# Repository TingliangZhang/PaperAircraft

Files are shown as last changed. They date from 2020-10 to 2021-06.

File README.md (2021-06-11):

# PaperAircraft
https://en.wikipedia.org/wiki/Paper_plane

## V3版本

全新版本

电磁舵机+8mm空心杯+1S小锂电+电磁舵机接收机（集成5A电调）

2.4G带两路电磁舵驱动 5通道微型接收机 Futaba S-FHSS

https://item.taobao.com/item.htm?id=544533760584

遥控器兼容 S-FHSS即可

https://futabausa.com/product/14sg/

## 纸飞机

https://www.poweruptoys.com/

https://www.indiegogo.com/projects/powerup-4-0-smartphone-controlled-paper-airplane--2#/

https://item.taobao.com/item.htm?id=598983848365

https://detail.1688.com/offer/623588992739.html

看了这么多产品，最后还是要自己写飞控。通信用蓝牙或者Wifi，NanoBLESense可能又要用起来了。

https://item.taobao.com/item.htm?id=580652831242

小巧的7.8g高压锂电还是要用的

1.7g微型舵机

https://item.taobao.com/item.htm?id=610628423127

参考F3P和F1D

F3P

https://ultralight.tech/

https://www.bilibili.com/video/BV1Yk4y1971W

F1D

https://www.bilibili.com/video/BV1Q5411s7f6

可以考虑用共轴反桨，但是重量有点大，如果能开发微型共轴反桨，可以搞简单的直升机雪花。

## 一些想法

激光切割卡纸

BLE广播 mesh

## V1方案

元件选型

主控板：[Arduino Nano 33 BLE Sense](https://store.arduino.cc/usa/nano-33-ble-sense-with-headers)

3.3V能否接3.8V+存疑，考虑换DCDC芯片，但是[MPM3610](https://www.monolithicpower.cn/cn/mpm3610.html)的封装是节省空间的 QFN-20 (3mmx5mmx1.6mm)封装，很难找到相应的芯片以及更换。此路不通

外接一块3.8v-3.3v DCDC转换模块，找了一圈淘宝，找到DM13B-3.3，可以升降压。

[Arduino Nano 33 BLE](https://store.arduino.cc/usa/nano-33-ble)更便宜

新解决方案！电调上面的UBEC，UBEC输出:5.2V 2A（正负0.1V），原本给接收机用的，可以用来驱动Arduino！

电池：[Happymodel 3.8V 300mAh 30C 1-2S Lipo Battery PH2.0 Plug for Mobula6/7](http://www.happymodel.cn/index.php/2018/09/22/happymodel-3-8v-300mah-30c-1-2s-lipo-battery-ph2-0-plug-for-mobula7/)

https://item.taobao.com/item.htm?id=580652831242

Capacity:300mAh

Voltage:3.8v

Continuous Discharge Rate: 30C

Instantaneous discharge rate: 60C

Size: 57mmx12mmx7mm

Weight: 6.5g

Connector: PH2.0

充电器：[Happymodel Mobula7 FPV Racing Drone Spare Part 1S06 6 Way Lipo/LIHV Battery Charger](http://www.happymodel.cn/index.php/2018/08/31/happymodel-ur65-fpv-racing-drone-spare-part-1s06-6-way-lipolihv-battery-charger/)

https://item.taobao.com/item.htm?id=566199133982

4.20v cell charging cutoff (+- 0.5% margin of error) for 1S Lipo Battery

4.35v cell charging cutoff (+- 0.5% margin of error) for 1S 3.8V LIHV Battery

电机：暂时使用劣质的1.72块钱一个的[高速航模电机马达双环强磁716空心杯电机3.7V暴力50000转包邮](https://item.taobao.com/item.htm?id=535704086171)

规格:7x16x0.8mm 额定电压：3.7V 启动电压：0.15V 额定电流：800mA 额定转速：34000

舵机：[AFRC-D1302微型1.7g舵机MINI精致1.9g航模室内飞机直升机数字舵机 ](https://item.taobao.com/item.htm?spm=a1z09.2.0.0.2afc2e8doX2vub&id=607309316067)

尺寸:13.5 x 6.2 x 20.1 mm

重量:1.7g(不含线)

工作电压:3.7~5.0V

扭力:

3.7V：2.08 oz-in (0.15 kg-cm)

4.2V：2.36 oz-in (0.17 kg-cm)
速度:

3.7V：0.06 sec/60°

4.2V：0.04 sec/60°

出线: JST1.25mm L=110mm （棕-，红+，橙S）

直线电机：[AFRC-D1015直线舵机1.5克微型轻量迷你1.5g数字舵机](https://item.taobao.com/item.htm?spm=a1z09.2.0.0.2afc2e8doX2vub&id=611726187447)

尺寸:21.4 x 15.2 x 6.0 mm

重量:1.5g(不含线)

出线: JST1.25mm L=100 mm （红+，黑-，白S）；JST1.0mm,JR,Futaba L=100 mm （棕-，红+，橙S）

工作电压:3.7~6.0V

工厂默认行程为7mm/900~2100us

电机驱动：[1S超小微型单向有刷电调航模飞机固定翼空心杯电机专用驱动控制器](https://item.taobao.com/item.htm?id=548195280709)

最多能接4个空心杯电机;N20,N30,N50,131,180电机可以接2只.。

输入电池电压:2.2V-5.2V（超过5.5V烧电调）.

最大输出电:流20A.

UBEC输出:5.2V 2A.（正负0.1V）

## V2做PCB方案

自己画：STM32 蓝牙 IMU

or ESP32WROOM + IMU

STM32选型：STM32G031K8T6 STM32G031J6M6

PCB板上外设：

1. 蓝牙透传
2. IMU（目前可选）
3. 3.8v-3.3v降压稳压芯片
4. 空心杯电机驱动芯片
5. 电池电机舵机接口

具体选型

### DCDC芯片

TI电源解决方案[选型](https://www.ti.com/design-resources/design-tools-simulation.html)网站

[WEBENCH Power Designer](http://webench.ti.com/power-designer/switching-regulator)

[TLV62569DBVR](https://item.szlcsc.com/153167.html) 2A

[TLV62568DBVR](https://item.szlcsc.com/174600.html) 1A

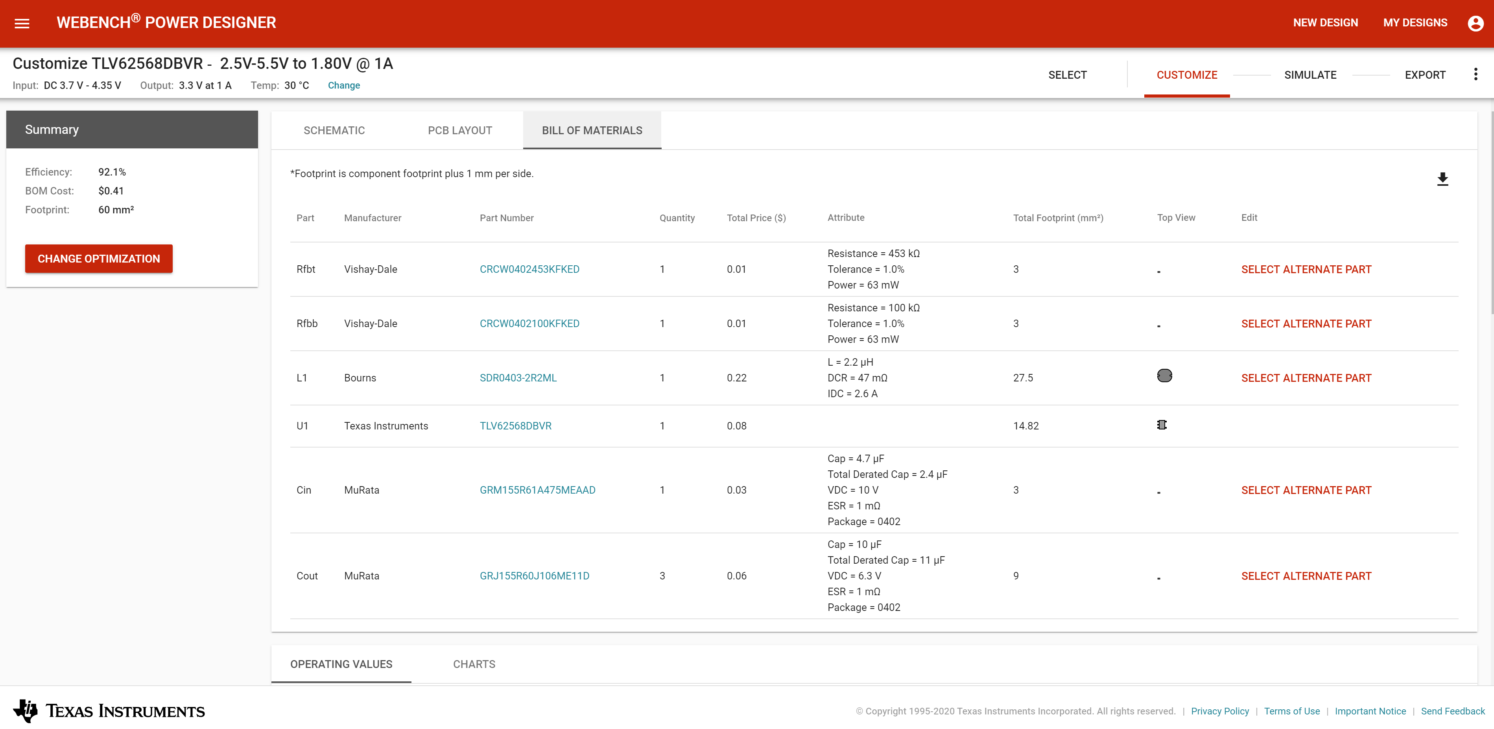
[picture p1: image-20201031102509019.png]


这个很好用，能生成原理图和BOM。

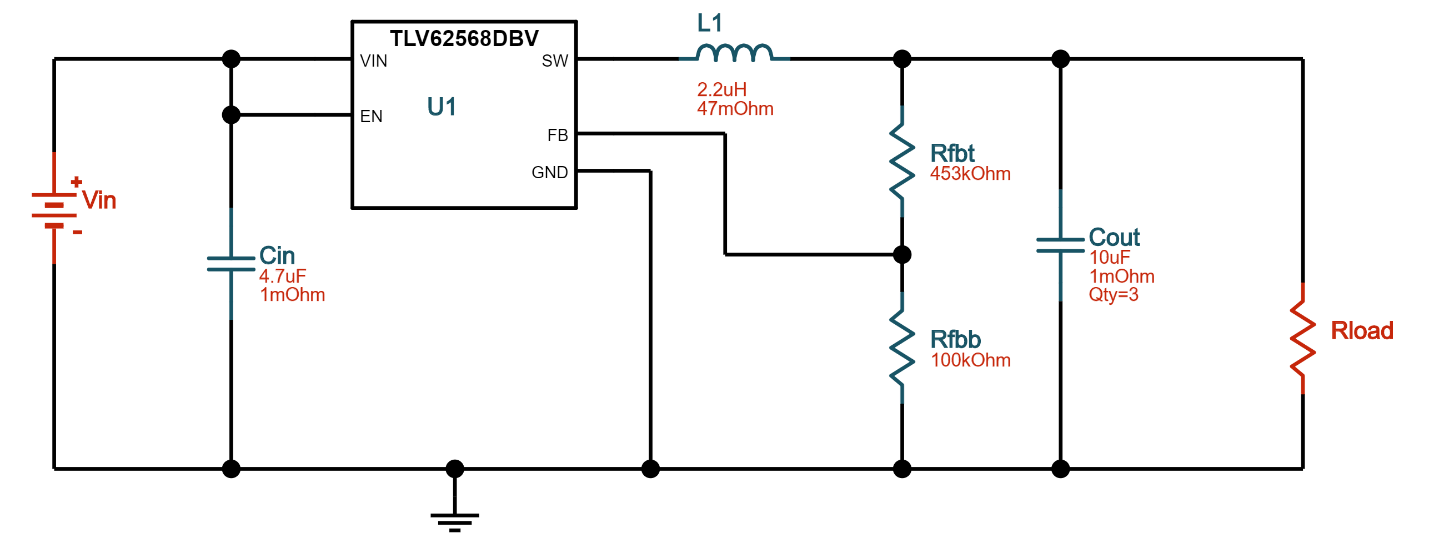
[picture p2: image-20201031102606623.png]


甚至仿真

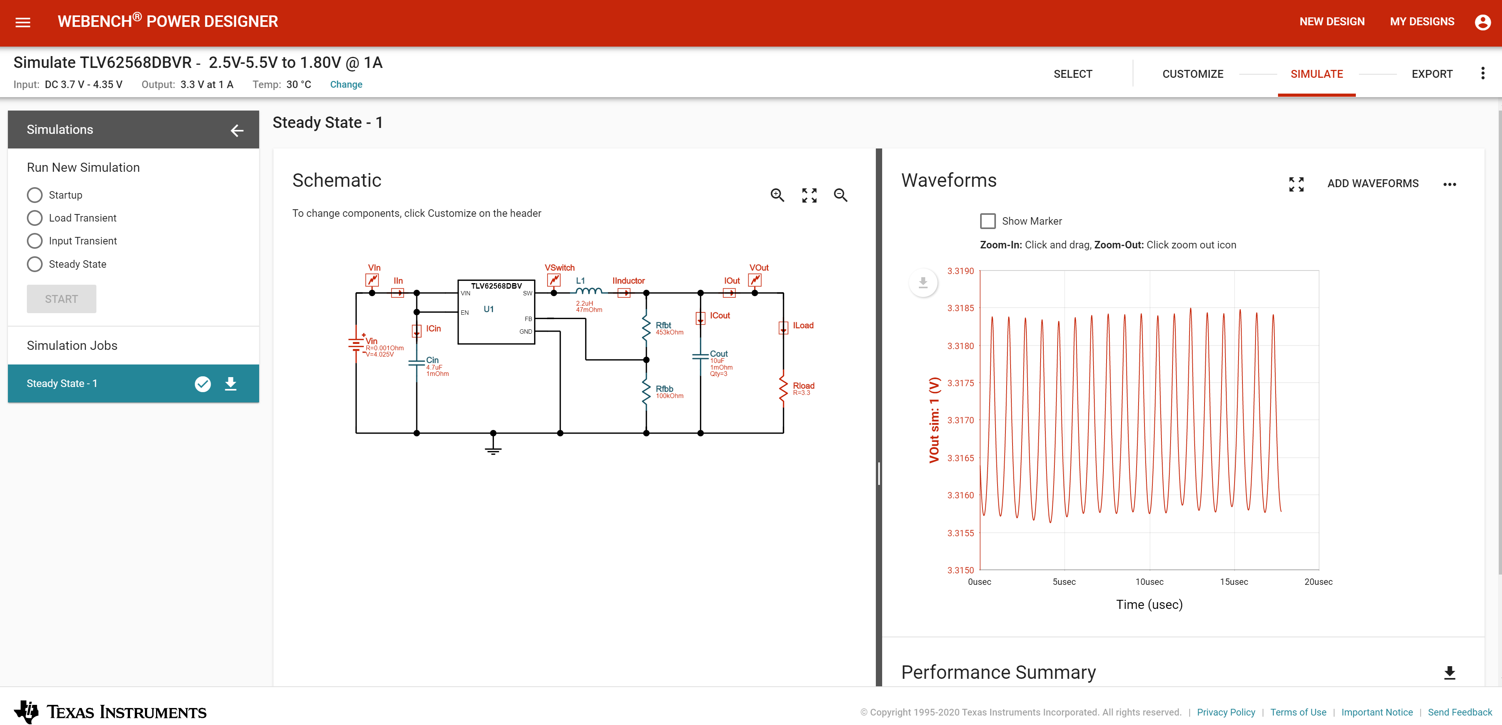
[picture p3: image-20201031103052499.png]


https://webench.ti.com/appinfo/webench/scripts/SDP.cgi?ID=C1D9EF81C082E009

TLV62568ADRLR及其周边电路BOM

[DC-DC芯片/TPS54331DR](https://item.szlcsc.com/10397.html)

[4.7uF(475) ±10% 10V](https://item.szlcsc.com/2057.html)

[10uF(106) ±20% 6.3V](https://item.szlcsc.com/2043.html)

[453KΩ ±1%](https://item.szlcsc.com/26561.html)

[100KΩ ±5%](https://item.szlcsc.com/16137.html)

[2.2uH ±20% 47mΩ 2.6A](https://item.szlcsc.com/503279.html)

[10uF(106) ±10% 10V](https://item.szlcsc.com/20411.html)无货更换为[10uF(106) ±20% 6.3V](https://item.szlcsc.com/2043.html)

### STM32

[STM32G031J6 ](https://www.st.com/en/microcontrollers-microprocessors/stm32g031j6.html)

Internal 16 MHz RC with PLL option 这玩意内部时钟16M感觉不用加外部时钟了，除非用得到48MHz

BOOT0用10k电阻拉低接地，boot from User Flash memory

加一个RST按钮，按下拉低RST

加入一个电源指示LED，以及一个接到PB9的LED

烧写用4pin杜邦线母头，接0/3.3V/TX/RX，使用ST-Link烧写程序

STM32G031J6及其周边电路BOM：

[STM32G031K8T6](https://item.szlcsc.com/428991.html)

[轻触开关 一型3x6x2.5有白ZD b拉伸白色按键 卷装](https://item.szlcsc.com/300030.html)

[1KΩ(1001) ±1%](https://item.szlcsc.com/116573.html)

[10KΩ(1002) ±1%](https://item.szlcsc.com/116572.html)

[100nF(104) ±10% 50V](https://item.szlcsc.com/1943.html)

[22Ω ±1%](https://item.szlcsc.com/24078.html)

[翠绿LED](https://item.szlcsc.com/207066.html)

可选晶振：[SMD3225 40.000MHZ 12PF 10PPM](https://item.szlcsc.com/420977.html)

### 电机驱动

[DRV8837CDSGR](https://item.szlcsc.com/213827.html)

### IMU

Arduino上面用的[LSM9DS1TR](https://www.digikey.cn/product-detail/zh/stmicroelectronics/LSM9DS1TR/497-14946-2-ND/4988083)在Digikey上面单个47.89块钱一个，太贵了

[MPU-6050](https://item.szlcsc.com/24852.html)嘉立创商城里也是10块钱左右

好贵，暂时不加了

### 蓝牙

都好贵，考虑ESP32了

[ESP32-WROOM-32](https://item.szlcsc.com/84060.html)

深圳大夏龙雀科技的蓝牙模块便宜点，十元以内

http://www.szdx-smart.com/

暂时选型[BT04-E低成本小体积无线串口透传蓝牙模组SPP3.0+BLE4.2蓝牙模块 ](https://item.taobao.com/item.htm?id=616730393533&_u=22q6uuheaa6e)

邮票孔版本。

Datasheet上面型号是，其实应该是Realtek RTL8762

本来想用[BT24高性价比串口高速透传BLE5.1微安级功耗蓝牙模块迷你无线模块](https://item.taobao.com/item.htm?id=621716432187&_u=22q6uuhea153)中的 DX-BT24-M[邮票孔贴片款] 但是不能更改参数，波特率或名字，就不太行。

封装用SOIC Footprint Wizard画

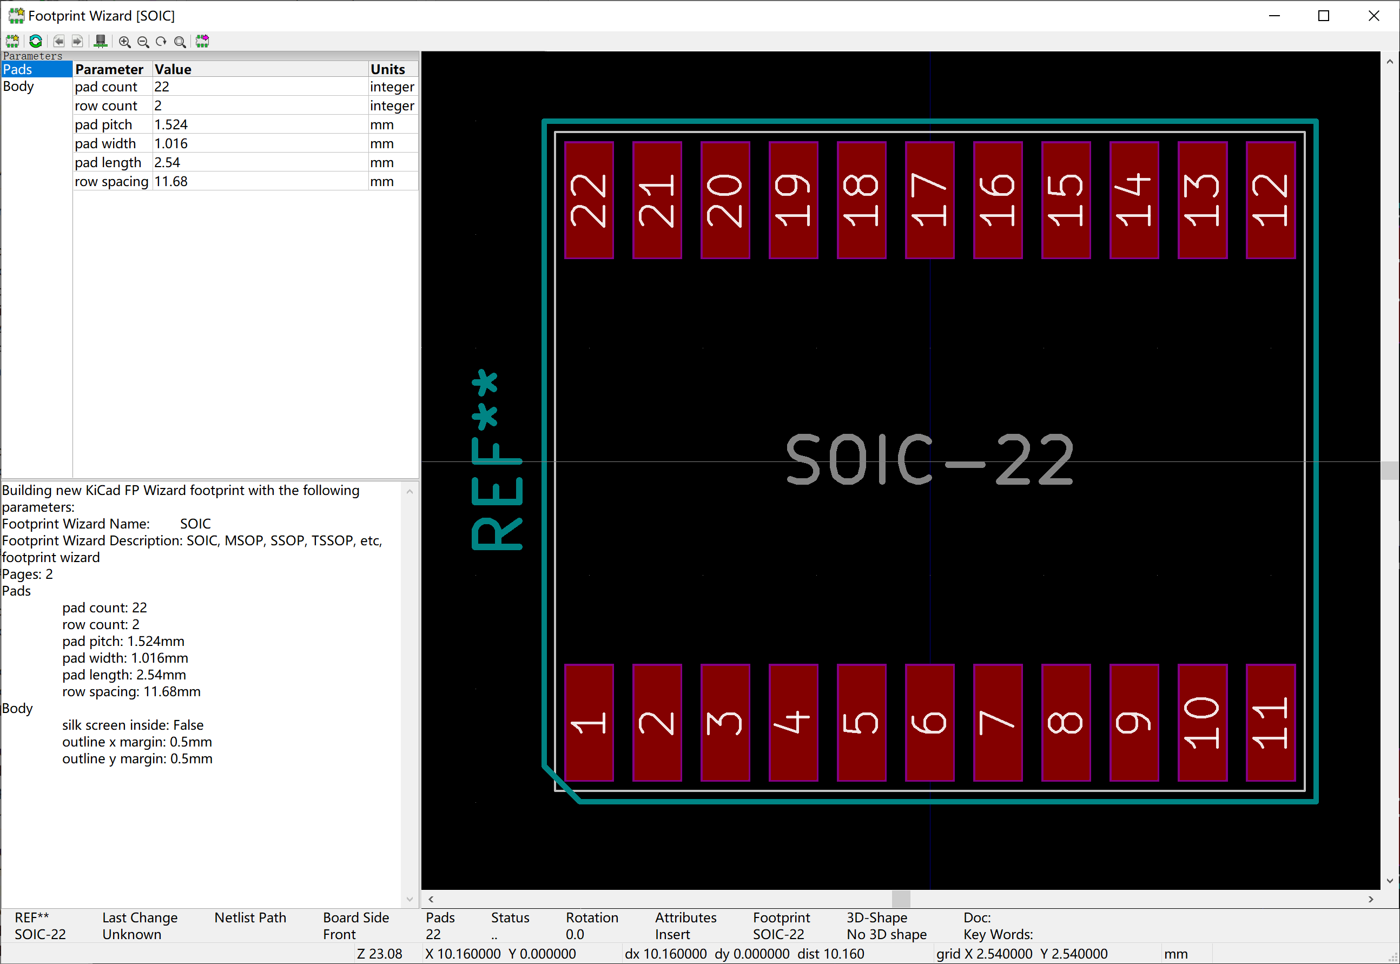
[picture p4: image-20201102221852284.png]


### 接口

电池接口选择PH2.0公头：[B2B-PH-K-S(LF)(SN)](https://item.szlcsc.com/142630.html)

电机接口 PH2.0公头：另一端需要母头压线端子 [PH2.0-T锡 编带](https://item.szlcsc.com/9392.html) 和胶壳 [胶壳 2.0mm 2Pin位](https://item.szlcsc.com/442393.html)

舵机接口 用[1.25T-1-3A](https://item.szlcsc.com/11366.html) 封装选用的Connector_Hirose:Hirose_DF13-03P-1.25DSA_1x03_P1.25mm_Vertical

烧写用4x2.54mm排针接在板上排母上[2.54x8.5排母 1x3P S/T](https://item.szlcsc.com/333717.html)

Futaba母头用3x2.54mm排针连接 [2.54-1*3P正弯针](https://item.szlcsc.com/93349.html)

## 气动设计

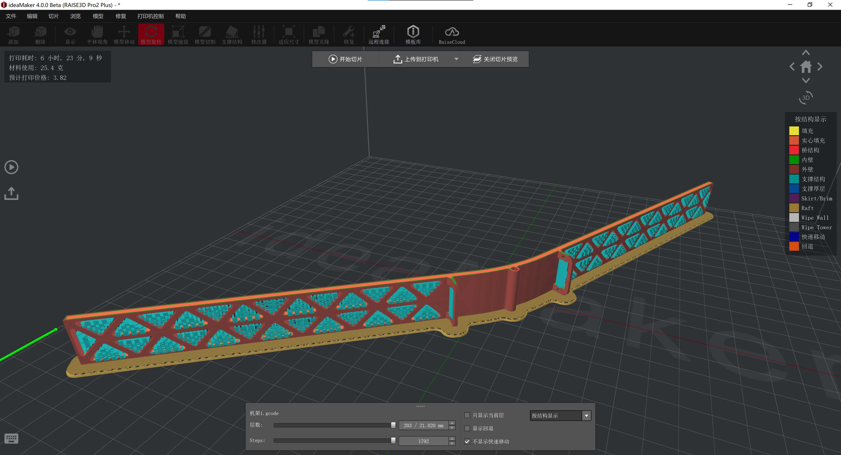
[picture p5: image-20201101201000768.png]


## 控制

### 舵机AFRC-D1302

[AFRC-D1302 Micro 1.7g Large Torque Mini Digital Servo for RC Airplane Fixed Wing Helicopter - JST 1.0 Plug](https://www.banggood.com/AFRC-D1302-Micro-1_7g-Large-Torque-Mini-Digital-Servo-for-RC-Airplane-Fixed-Wing-Helicopter-p-1618521.html?ID=6285197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)

这俩都是333Hz，所以3ms周期，0.9-2.1ms对应-55到55 degree角度。

裂开了，这玩意真的是3ms，不是20ms周期！

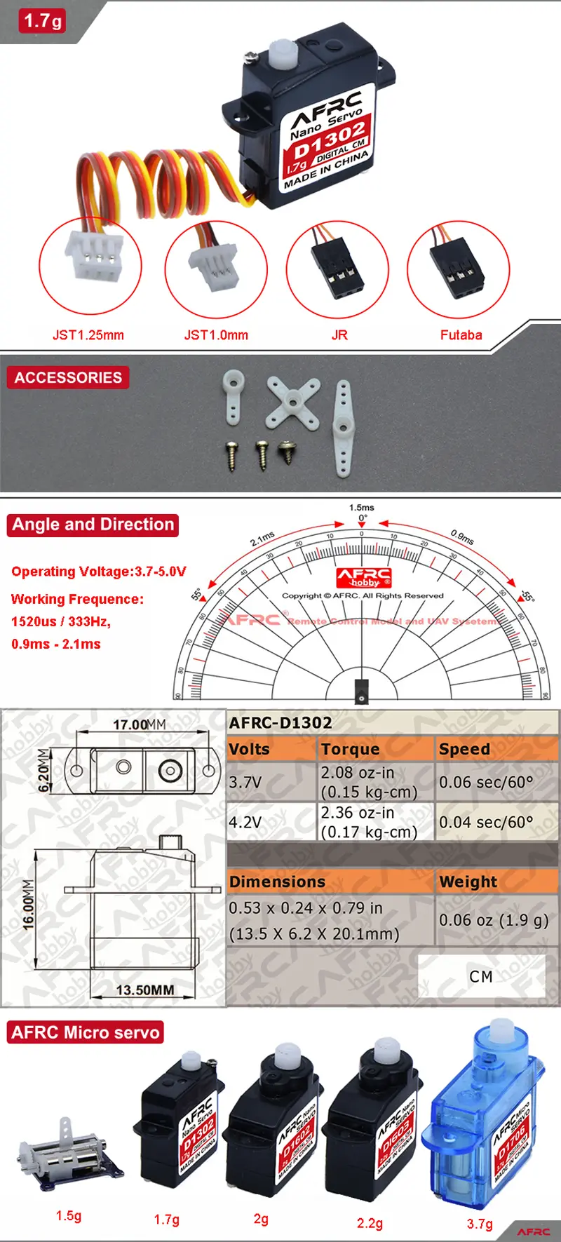
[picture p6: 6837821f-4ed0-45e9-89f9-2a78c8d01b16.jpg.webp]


太邪教了，换一个正常点的舵机：[2.2克超微型数字舵机 PZ-15318](https://item.taobao.com/item.htm?spm=a1z09.2.0.0.334a2e8dFbH5WX&id=591162573182&_u=32q6uuhe6ed0)

PWM, 50HZ， 高电平时间在1~2ms

工作电压：2.5V-4.8V

注意不到5V，不能接到Arduino5V端口。

### 直线电机AFRC-D1015

[AFRC-D10115 1.5g Linear Servo Miniature Micro Lightweight with Digital Controller for AFRC-D1015 Indoor 3D Small RC Aircraft - JR Plug](https://www.banggood.com/AFRC-D10115-1_5g-Linear-Servo-Miniature-Micro-Lightweight-with-Digital-Controller-for-AFRC-D1015-Indoor-3D-Small-RC-Aircraft-p-1619274.html?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)

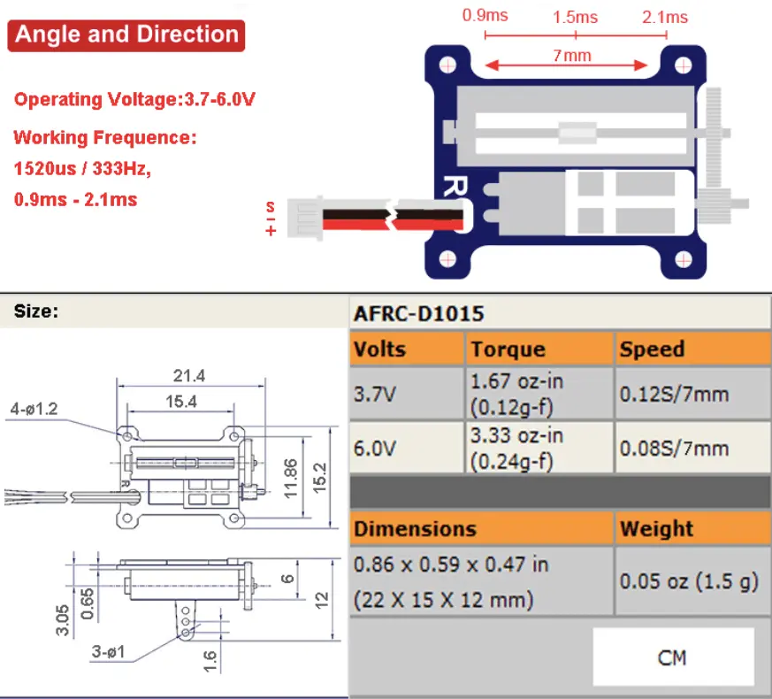
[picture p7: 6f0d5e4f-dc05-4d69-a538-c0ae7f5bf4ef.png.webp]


### 电机和驱动

正常电调的控制信号范围是1000us到2000us，一个周期20ms。

买的这个是直流有刷电机电调

用[Servo](https://www.arduino.cc/reference/en/libraries/servo/)库

```c
servo.attach(pin, min, max);
myservo.write(angle); // set servo to 0 - 180
```

拔了USB之后电机就转了23333

更精确控制用

```c
myservo.writeMicroseconds(1500);  // set servo to mid-point
```

### 蓝牙

The communications chipset on the Nano 33 BLE can be both a BLE and Bluetooth client and host device. Something pretty unique in the world of microcontroller platforms. If you want to see how easy it is to create a Bluetooth central or a peripheral device, explore the examples at our [ArduinoBLE library](https://www.arduino.cc/en/Reference/ArduinoBLE).

classic参考

[Arduino Bluetooth Basic Tutorial](https://create.arduino.cc/projecthub/mayooghgirish/arduino-bluetooth-basic-tutorial-d8b737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)

BLE参考

[Arduino BLE Example Explained Step by Step](https://rootsaid.com/arduino-ble-example/)

[Arduino BLE Accelerometer Tutorial for Beginners](https://rootsaid.com/arduino-ble-accelerometer-tutorial/)

注意：电脑中打开串口监视器才启动蓝牙设备Bluetooth device active, waiting for connections...

You can use a generic BLE central app, like LightBlue (iOS and Android) or nRF Connect (Android), to interact with the services and characteristics created in this sketch.

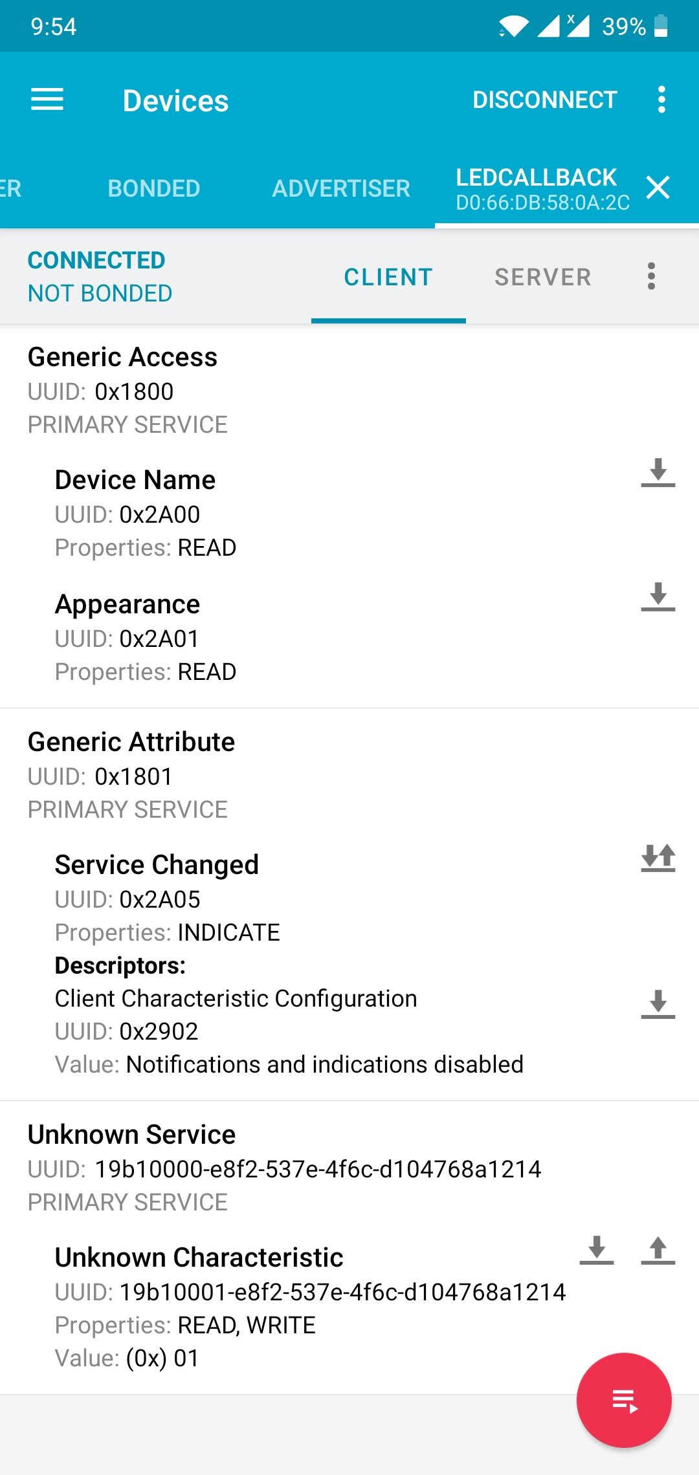
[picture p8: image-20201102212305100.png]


[Using Bluetooth 4.0 "classic" with Arduino Nano 33 BLE?](https://forum.arduino.cc/index.php?topic=649306.msg4378833#msg4378833)

绝望，没有 bluetooth classic ，BLE连不上Bluetooth Electronics，所以没办法搞GUI。

### IMU

[Arduino_LSM9DS1](https://github.com/arduino-libraries/Arduino_LSM9DS1)Allows you to read the accelerometer, magnetometer and gyroscope values from the LSM9DS1 IMU on your Arduino Nano 33 BLE Sense.

### ESP32

[ESP32 BLE Arduino](https://www.arduino.cc/reference/en/libraries/esp32-ble-arduino/)

### 蓝牙模块

模块未连接时为AT 模式，连接上后为透传模式

## 程序编写

Arduino端的程序就是读取UART，操控舵机和电机，手机端的Bluetooth Electronics可以定义UI推杆和摇杆，并且可以定义开始位和结束位。

Serial是USB，Serial1是D0 and D1即TX RX。

[Serial](https://www.arduino.cc/reference/en/language/functions/communication/serial/) Reference

一个Servo库的bug，我调了半天最后，更新了一下下Servo库，就好了。。。

AXY算出来多了528......原因未知。先减528再说。。。。。

## 涉及软件

Kicad

[Fritzing](https://fritzing.org/)

官网下载要8欧，直接Github[fritzing-app](https://github.com/fritzing/fritzing-app)中找到[CD-548](https://github.com/fritzing/fritzing-app/releases/tag/CD-548)发布0.9.5

http://fritzing.org/download/0.9.3b/windows-64bit/fritzing.0.9.3b.64.pc.zip

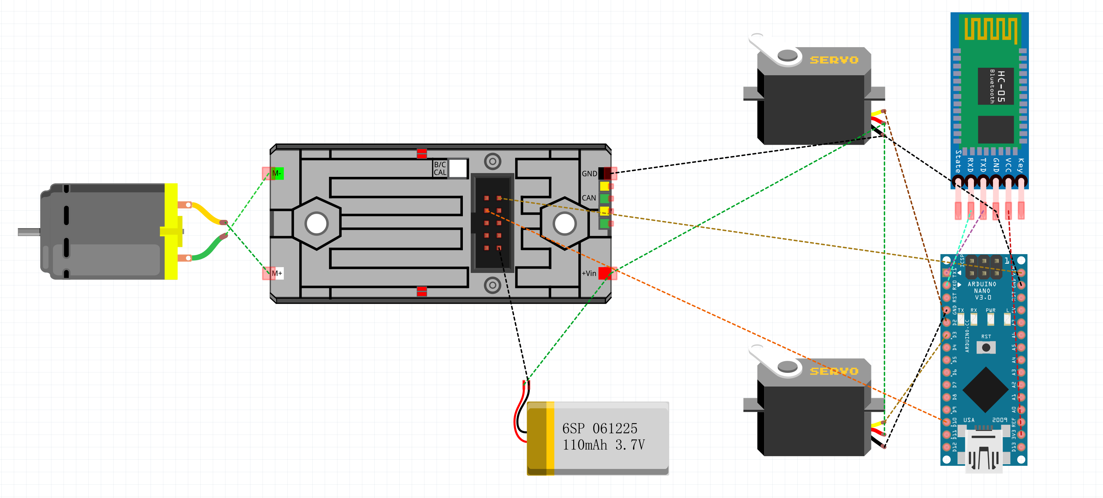
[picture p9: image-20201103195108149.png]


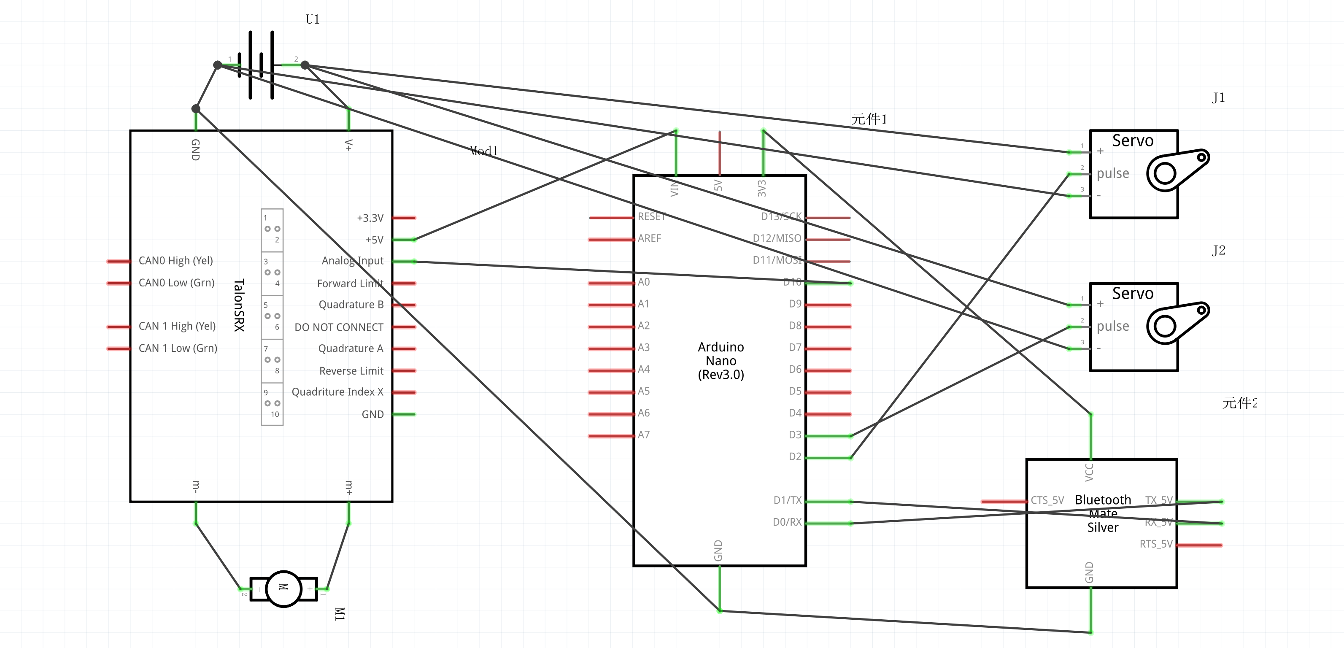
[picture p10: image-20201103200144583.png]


## 调试

螺旋桨or电风扇

竟然螺旋桨是反着吹的。我说怎么打死飞不起来。。。



20201104 22：30 第一次完整程序测试，电调灯时亮时灭，有短路。舵机只有一个转，另一个不转，可能是代码有问题或者舵机坏了。查了没发现代码问题，明天早上去换一下看看转不转。

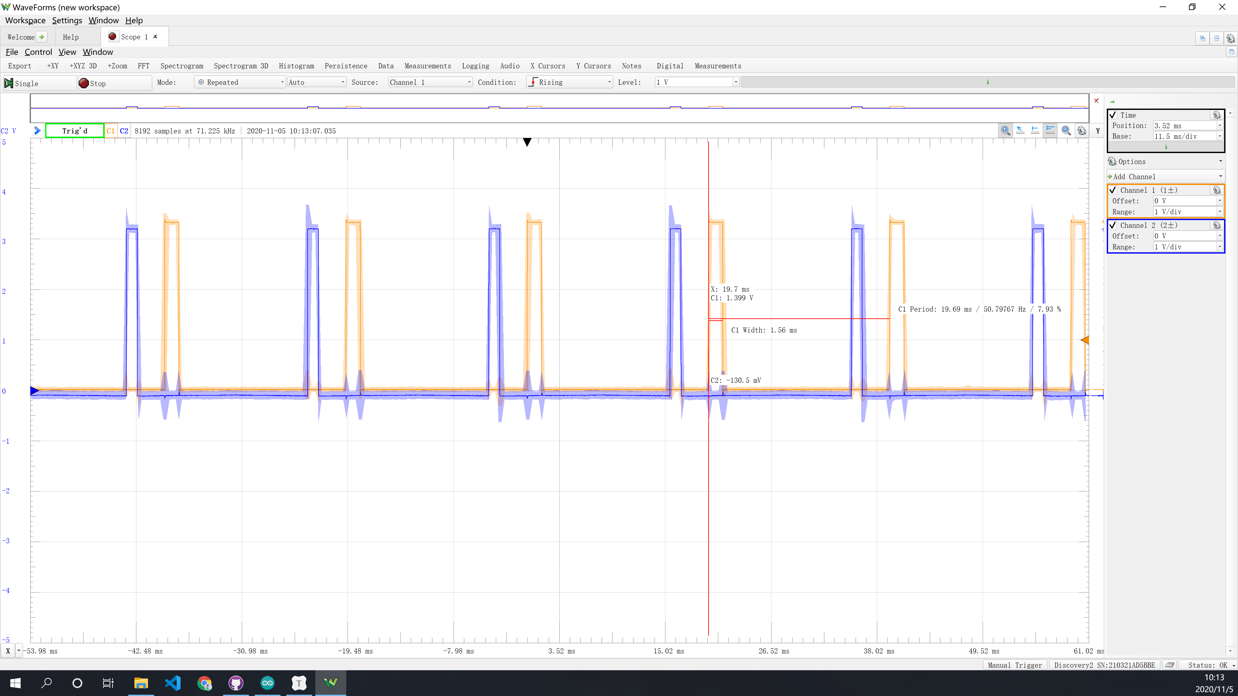
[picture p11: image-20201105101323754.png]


波形信号都对。最终发现是电调的连接线掉了。。。以及舵机本身就是3ms的周期，现在写的是20ms，等新的舵机到。

新的舵机到了，很好用。

电机到75%才开始转，而且没看出来调速功能，以及转的不如直接接电池快。

破案了：75的时候电调才开始被驱动，76的时候信号灯才亮。

尝试发现信号范围竟然是1800-2300us。。。

20201106连不上BT04-E问题解决：先配对，之后用nRF Connect连接一次，关闭程序后，用Bluetooth Electronics连接，不行就重启

### Bluetooth Electronics APP内设置

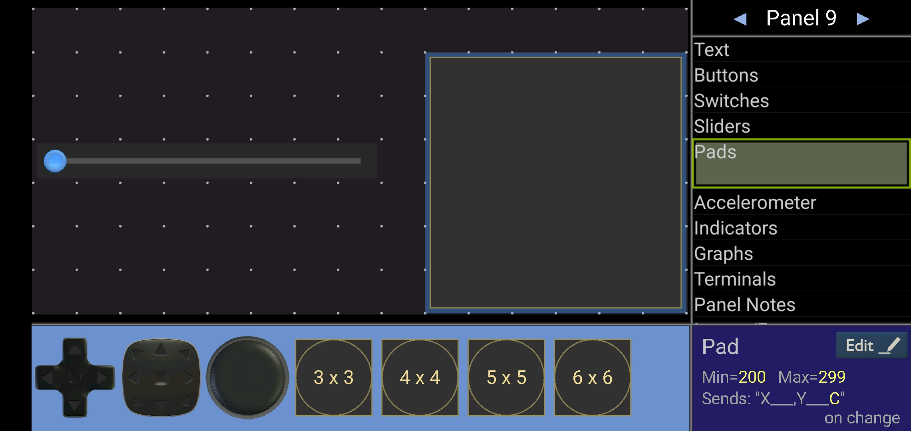
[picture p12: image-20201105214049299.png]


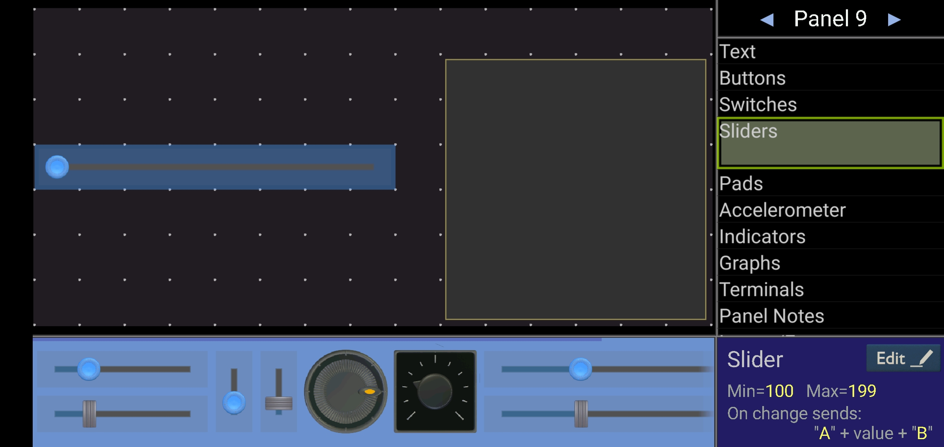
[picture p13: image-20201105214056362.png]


## V2成果







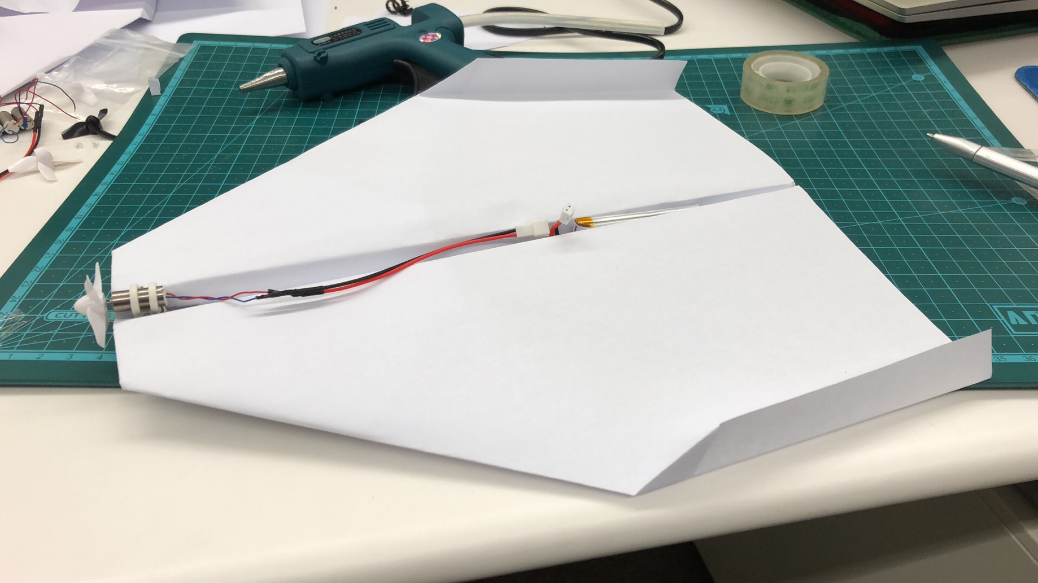
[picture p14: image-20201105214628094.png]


## Seeeduino XIAO

[Seeeduino XIAO - Arduino Microcontroller - SAMD21 Cortex M0+](https://www.seeedstudio.com/Seeeduino-XIAO-Arduino-Microcontroller-SAMD21-Cortex-M0+-p-4426.html)

This is the [Wiki](http://wiki.seeedstudio.com/Seeeduino-XIAO/) of the Seeeduino XIAO

## PCB设计

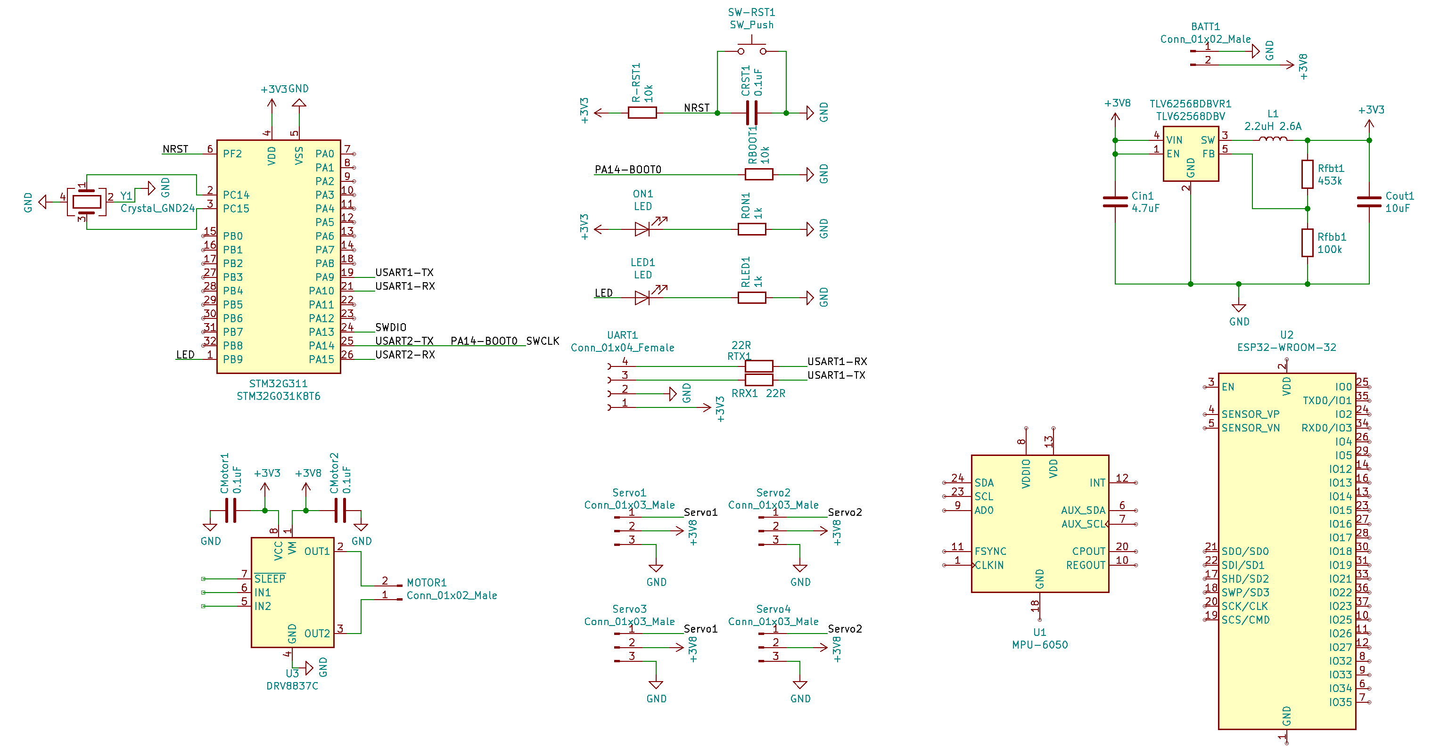
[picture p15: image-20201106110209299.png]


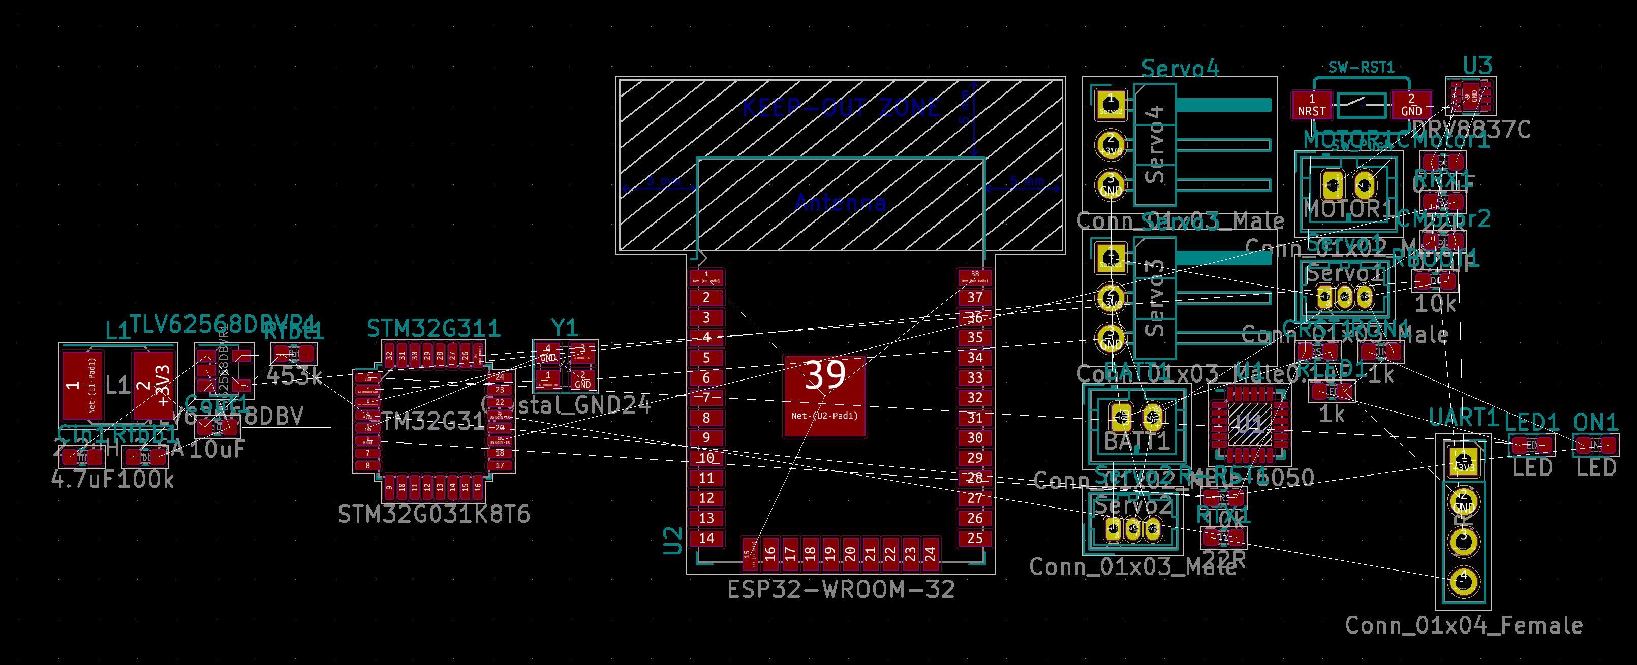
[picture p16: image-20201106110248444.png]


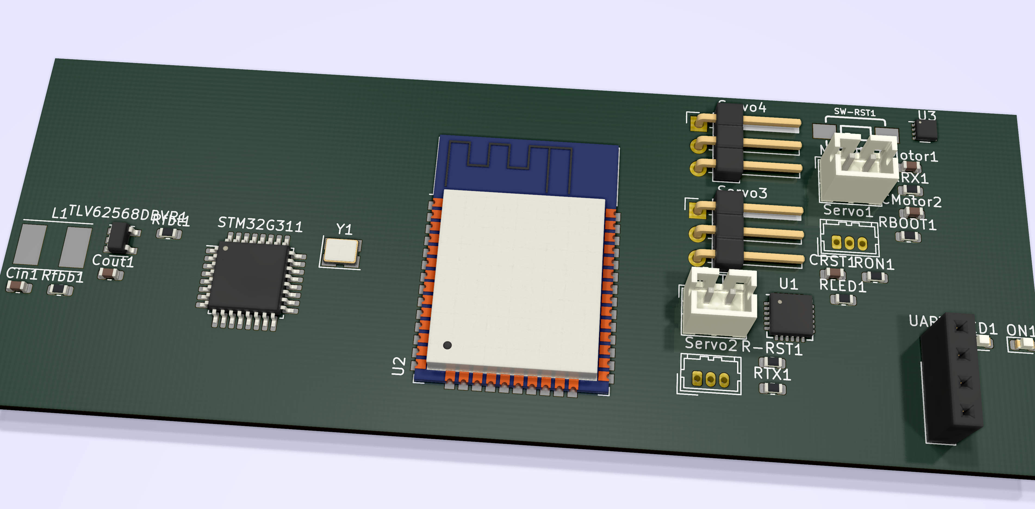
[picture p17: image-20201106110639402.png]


## V3成本估计

控制成本到10元级别，选用STM32G031K8T6或ESP32-WROOM-32，DRV8837C，TLV62568DBV

| 品名 | 目前购买价（RMB） | 量产价 |
| --- | --- | --- |
| [ICM-20600](https://invensense.tdk.com/products/motion-tracking/6-axis/icm-20600/) | 1.38 | |
| STM32G031K8T6 | 4.81 | |
| DRV8837C | 0.5561 | |
| TLV62568DBV | 1.0181 | |
| 其他连接件3D打印 | 2 | |
| PCB | 1 | |

## V2时间线

| 倒计时N天 | 肝的活 |
| --- | --- |
| 7 | 确定做纸飞机，选型V1核心板，设计大致的架构 |
| 6 | 开始担心重量问题，画了V2的PCB，jlc买元件，赶着下打样订单，蓝牙HC-05和IMU-6050太贵，暂时没找到便宜的，没画完。 |
| 5 | 大批购买元件，顺丰空运要第二天到，利用手头的元件测试舵机。叠各种构型纸飞机载重试飞，确定上反角+翼尖小翼气动构型。 |
| 4 | 2.2g舵机和BT-04E到货，调蓝牙通信，以及供电解决方案，通过电调解决。 |
| 3 | 测试整体系统成功，代码整体测试通过。 |
| 2 | 焊了一天的线，BT04模块贴片引脚太小了，焊了俩小时，小体积的 |
| 1 | 上午整机组装试飞，拍视频。 |

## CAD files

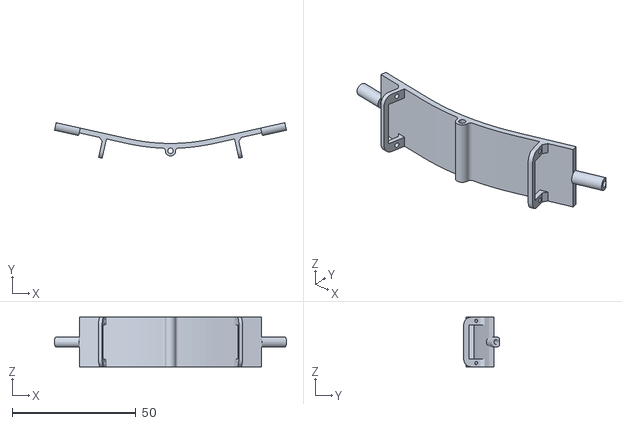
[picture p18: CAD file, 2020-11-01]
3Dmodel/机架2.STL
93.7 x 14.4 x 20.0

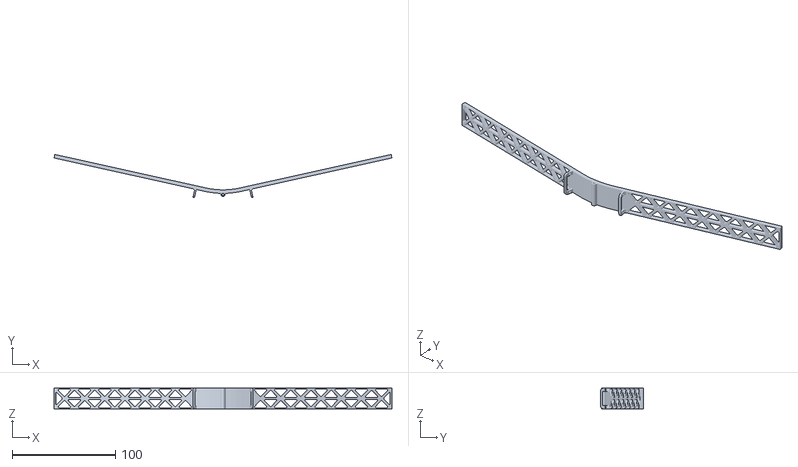
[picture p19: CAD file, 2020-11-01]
3Dmodel/机架01.STL
327.5 x 41.8 x 20.0

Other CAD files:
3Dmodel/UM3E_机架2.3mf

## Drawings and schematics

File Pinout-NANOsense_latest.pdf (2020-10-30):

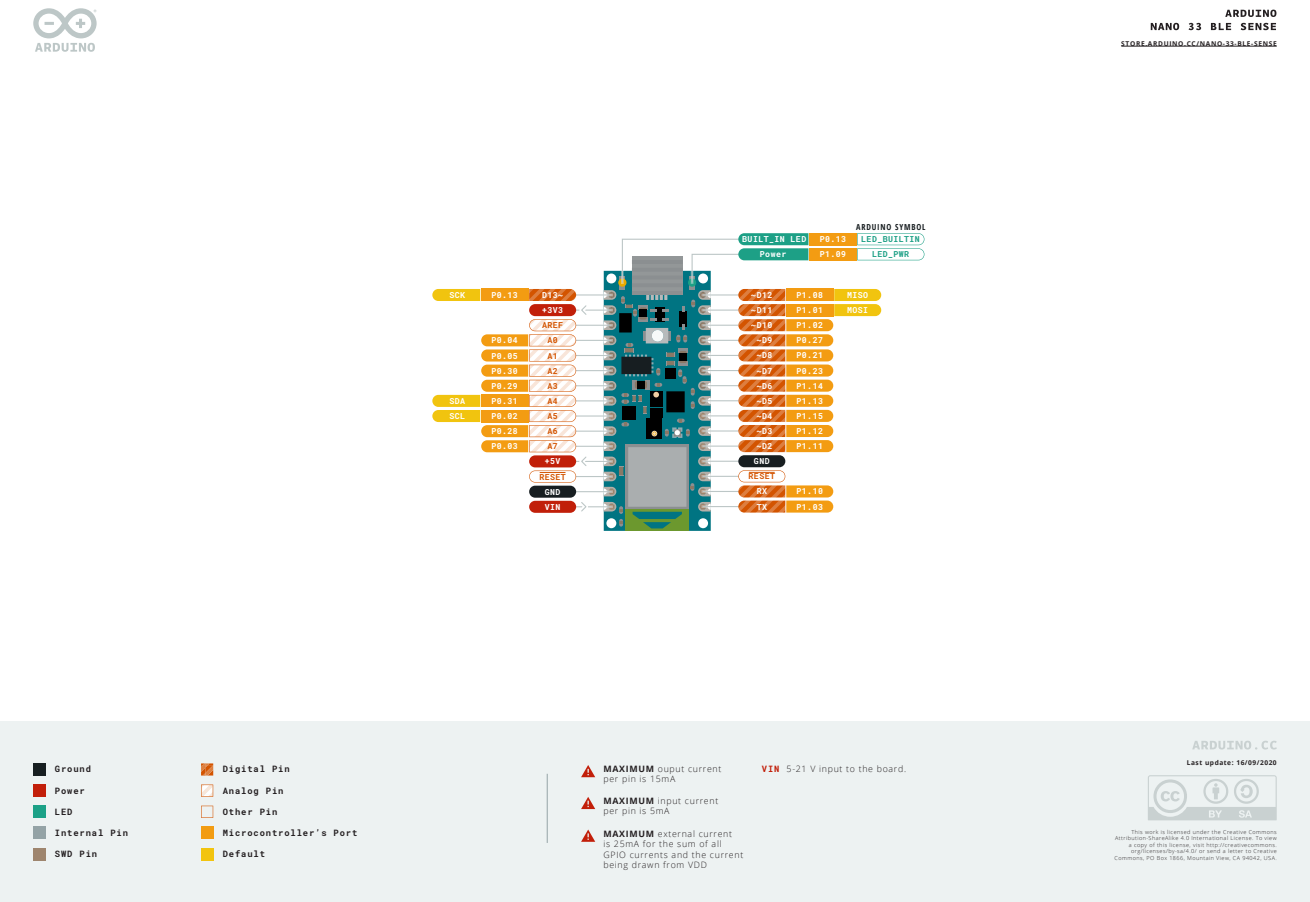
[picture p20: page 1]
Ground; Power; LED; Internal Pin; SWD Pin; Digital Pin; Analog Pin; Other Pin; Microcontroller’s Port; Default; Last update: 16/09/2020; GND; MISO MOSI; +3V3 AREF; GND VIN; SCK; SDA SCL; RESET; BUILT_IN LED; ARDUINO SYMBOL; LED_PWR; LED_BUILTIN

STORE.ARDUINO.CC/NANO-33-BLE-SENSE (https://store.arduino.cc/arduino-nano-33-ble-sense)

MAXIMUM ouput current
per pin is 15mA
MAXIMUM input current
per pin is 5mA

VIN 5-21 V input to the board.

MAXIMUM external current
is 25mA for the sum of all
GPIO currents and the current
being drawn from VDD

This work is licensed under the Creative Commons
Attribution-ShareAlike 4.0 International License. To view
a copy of this license, visit http://creativecommons.
org/licenses/by-sa/4.0/ or send a letter to Creative
Commons, PO Box 1866, Mountain View, CA 94042, USA.

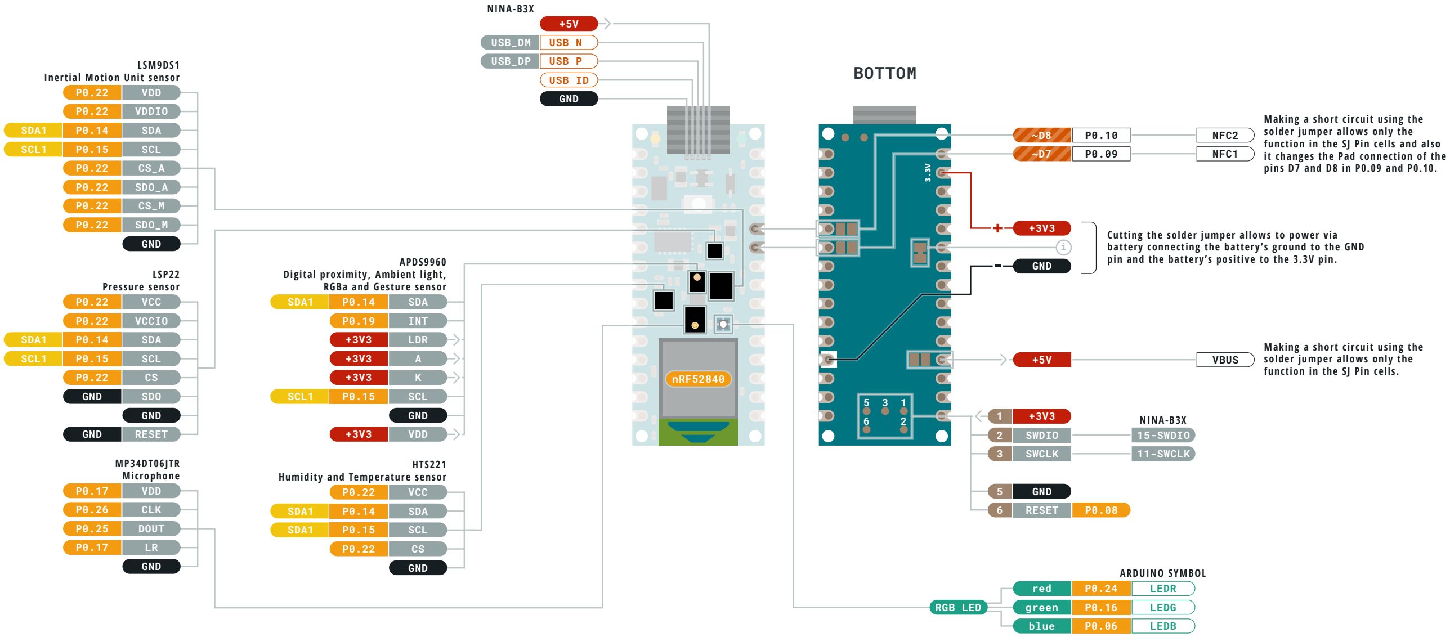
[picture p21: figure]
BOTTOM; SWDIO SWCLK; GND; VBUS; 15-SWDIO 11-SWCLK; NINA-B3X; VDD; VDDIO; SDA1; SDA; SCL1; SCL; SDO_A; SDO_M; LSM9DS1 Inertial Motion Unit sensor; INT; LDR; APDS9960 Digital proximity, Ambient light, RGBa and Gesture sensor; VCC; SDA1 SDA1; HTS221 Humidity and Temperature sensor; VCCIO; SDO; RESET; LSP22 Pressure sensor; CLK; DOUT; MP34DT06JTR Microphone; Making a short circuit using the solder jumper allows only the function in the SJ Pin cells.; USB N; USB P USB ID GND; USB_DM USB_DP; NFC2 NFC1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
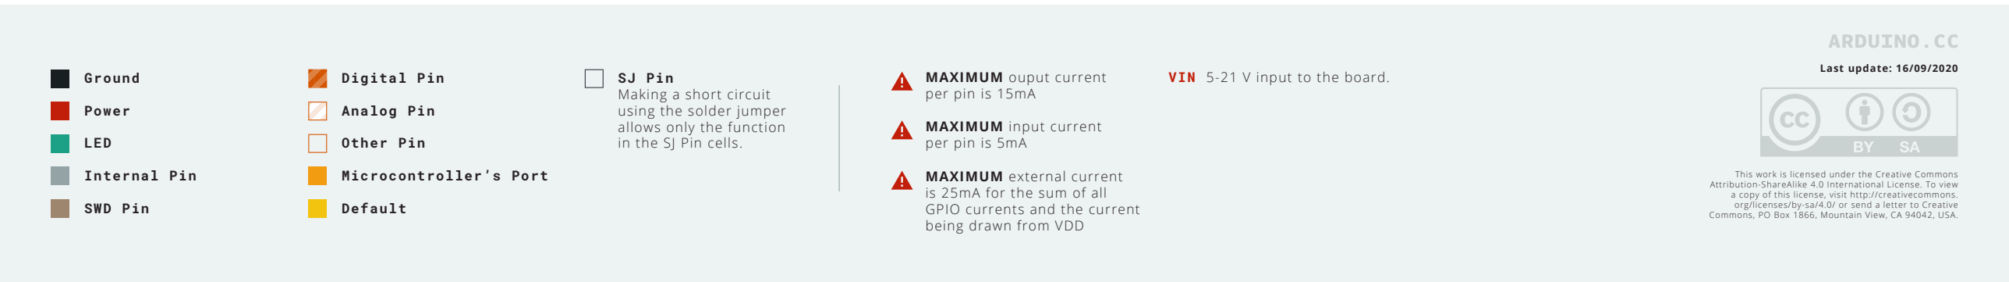
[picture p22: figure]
Ground; Power; LED; Internal Pin; SWD Pin; SJ Pin Making a short circuit using the solder jumper allows only the function in the SJ Pin cells.; Digital Pin; Analog Pin; Other Pin; Microcontroller’s Port; Default; Last update: 16/09/2020; MAXIMUM input current per pin is 5mA; MAXIMUM external current is 25mA for the sum of all GPIO currents and the current being drawn from VDD; MAXIMUM ouput current per pin is 15mA; VIN 5-21 V input to the board.

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

Cutting the solder jumper allows to power via battery connecting the battery’s ground to the GND pin and the battery’s positive to the 3.3V pin.

STORE.ARDUINO.CC/NANO-33-BLE-SENSE (https://store.arduino.cc/arduino-nano-33-ble-sense)

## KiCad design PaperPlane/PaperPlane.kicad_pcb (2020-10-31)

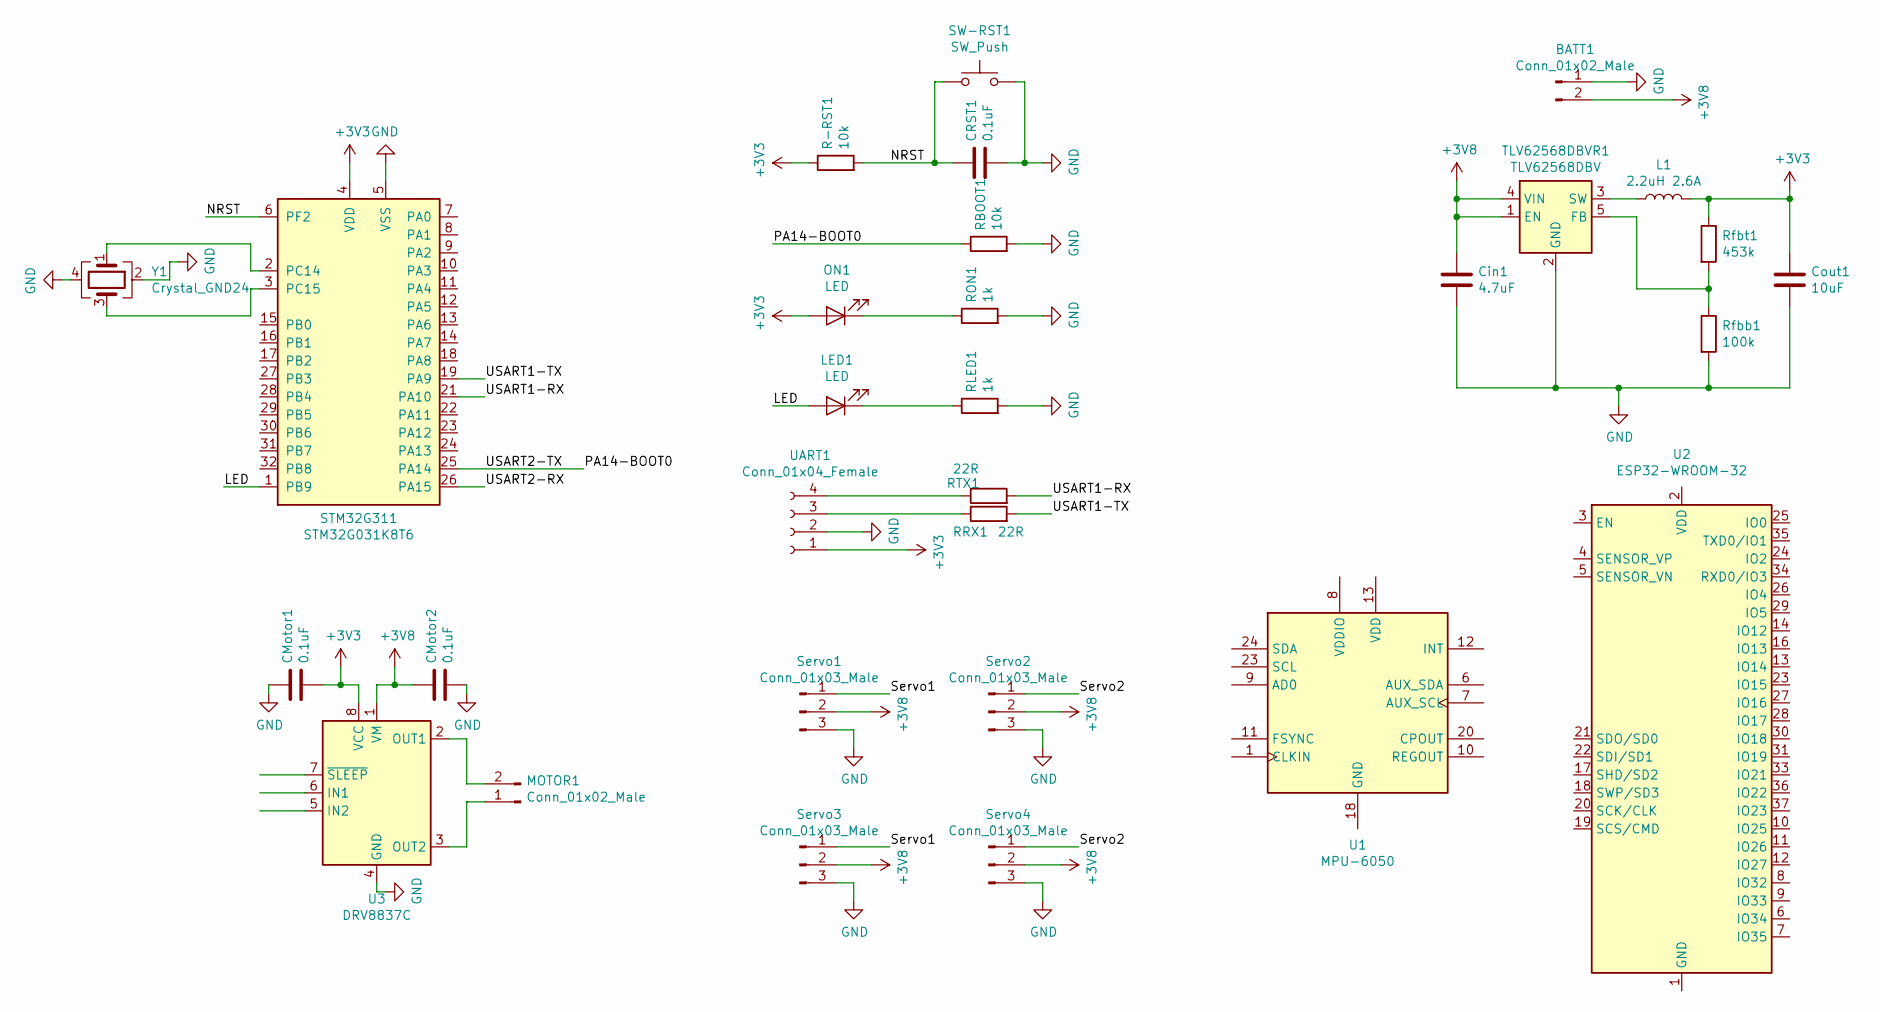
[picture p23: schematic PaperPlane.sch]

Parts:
BATT1: Conn_01x02_Male; JST_PH_B2B-PH-K_1x02_P2.00mm_Vertical
CMotor1, CMotor2: 0.1uF; C_0603_1608Metric
CRST1: 0.1uF; C_0603_1608Metric
Cin1: 4.7uF; C_0603_1608Metric
Cout1: 10uF; C_0603_1608Metric
L1: 2.2uH 2.6A; L_Taiyo-Yuden_NR-50xx_HandSoldering
LED1: LED; LED_0603_1608Metric
MOTOR1: Conn_01x02_Male; JST_PH_B2B-PH-K_1x02_P2.00mm_Vertical
ON1: LED; LED_0603_1608Metric
R-RST1: 10k; R_0603_1608Metric
RBOOT1: 10k; R_0603_1608Metric
RLED1: 1k; R_0603_1608Metric
RON1: 1k; R_0603_1608Metric
RRX1: 22R; R_0603_1608Metric
RTX1: 22R; R_0603_1608Metric
Rfbb1: 100k; R_0603_1608Metric
Rfbt1: 453k; R_0603_1608Metric
STM32G311: STM32G031K8T6; LQFP-32_7x7mm_P0.8mm
SW-RST1: SW_Push; TACTILE_SWITCH_SMD_6.0X3.5MM
Servo1, Servo2: Conn_01x03_Male; Hirose_DF13-03P-1.25DSA_1x03_P1.25mm_Vertical
Servo3, Servo4: Conn_01x03_Male; PinHeader_1x03_P2.54mm_Horizontal
TLV62568DBVR1: TLV62568DBV; SOT-23-5
U1: MPU-6050; InvenSense_QFN-24_4x4mm_P0.5mm
U2: ESP32-WROOM-32
U3: DRV8837C; WSON-8-1EP_2x2mm_P0.5mm_EP0.9x1.6mm
UART1: Conn_01x04_Female; PinSocket_1x04_P2.54mm_Vertical
Y1: Crystal_GND24; Crystal_SMD_3225-4Pin_3.2x2.5mm

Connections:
+3V3: CMotor1.2, Cout1.1, L1.2, ON1.2 (A), R-RST1.1, Rfbt1.1, STM32G311.4 (VDD), U3.8 (VCC), UART1.1
+3V8: BATT1.2, CMotor2.1, Cin1.1, Servo1.2, Servo2.2, Servo3.2, Servo4.2, TLV62568DBVR1.1 (EN), TLV62568DBVR1.4 (VIN), U3.1 (VM)
/LED: LED1.2 (A), STM32G311.1 (PB9)
/NRST: CRST1.1, R-RST1.2, STM32G311.6 (PF2), SW-RST1.1
/PA14-BOOT0: RBOOT1.1, STM32G311.25 (PA14)
/Servo1: Servo1.1, Servo3.1
/Servo2: Servo2.1, Servo4.1
/USART1-RX: RTX1.2, STM32G311.21 (PA10)
/USART1-TX: RRX1.2, STM32G311.19 (PA9)
GND: BATT1.1, CMotor1.1, CMotor2.2, CRST1.2, Cin1.2, Cout1.2, RBOOT1.2, RLED1.2, RON1.2, Rfbb1.2, STM32G311.5 (VSS), SW-RST1.2, Servo1.3, Servo2.3, Servo3.3, Servo4.3, TLV62568DBVR1.2 (GND), U3.4 (GND), U3.9 (GND), UART1.2, Y1.2, Y1.4
unnamed: L1.1, TLV62568DBVR1.3 (SW)
unnamed: LED1.1 (K), RLED1.1
unnamed: MOTOR1.1, U3.3 (OUT2)
unnamed: MOTOR1.2, U3.2 (OUT1)
unnamed: ON1.1 (K), RON1.1
unnamed: RRX1.1, UART1.3
unnamed: RTX1.1, UART1.4
unnamed: Rfbb1.1, Rfbt1.2, TLV62568DBVR1.5 (FB)
unnamed: STM32G311.2 (PC14), Y1.1
unnamed: STM32G311.3 (PC15), Y1.3
unnamed: U2.1 (GND), U2.15 (GND), U2.38 (GND), U2.39 (GND)

Board: 2 copper layers, 30 parts (0 on the bottom side), 21 nets, no tracks yet.

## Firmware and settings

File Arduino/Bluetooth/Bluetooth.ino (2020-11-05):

#include <stdio.h>
#include <string.h>
#include <Servo.h>

Servo myservoX;  // create servo object to control a servo
Servo myservoY;  // create servo object to control a servo
Servo mymotor;   // create servo object to control a motor
// twelve servo objects can be created on most boards

int A = 0; //Motor Speed Control
int X = 0; //Left Servo Control
int Y = 0; //Right Servo Control

int B = 0; //Reverse
int C = 0; //Reverse

int GotInt = 0; //GetInt function return

int x[3] = {0,0,0};
int y[3] = {0,0,0};
int a[3] = {0,0,0};
int count = 0; //count for Input to AXY

void setup() {
  Serial.begin(9600);
  Serial1.begin(9600);

  myservoX.attach(2);  // attaches the servo on pin D2 to the servo object
  myservoY.attach(3);  // attaches the servo on pin D3 to the servo object
  mymotor.attach(10);  // attaches the motor on pin D10 to the servo object
}

void loop() {
//  if (Serial.available()) {      // If anything comes in Serial (USB),
//    Serial1.write(Serial.read());   // read it and send it out Serial1 (pins 0 & 1)
//  }
//  if (Serial1.available()) {     // If anything comes in Serial1 (pins 0 & 1)
//    Serial.write(Serial1.read());   // read it and send it out Serial (USB)
//  }


  if (Serial1.available()) {     // If anything comes in Serial1 (pins 0 & 1)
//     char Input = Serial1.read();
//     Serial.print(Input);   // read it and send it out Serial (USB)
//     Serial.print("\n");        //New line 

//     Serial.write(Serial1.read());
     
     char Input = Serial1.read();
    
     switch(count){
        case 1:
          x[0] = Input;
          count++;
          break;
        case 2:
          x[1] = Input;
          count++;
          break;
        case 3:
          x[2] = Input;
          X = int(x[1])*10+int(x[2])-528;
          myServoX(X);
          count=0;
          break;
        case 4:
          y[0] = Input;
          count++;
          break;
        case 5:
          y[1] = Input;
          count++;
          break;
        case 6:
          y[2] = Input;
          Y = int(y[1])*10+int(y[2])-528;
          myServoY(Y);
          count=0;
          break;
        case 7:
          a[0] = Input;
          count++;
          break;
        case 8:
          a[1] = Input;
          count++;
          break;
        case 9:
          a[2] = Input;
          A = int(a[1])*10+int(a[2])-528;
          myMotor(A);
          count=0;
          break;
     }
     if(Input=='X'){
         count=1;
     }
     if(Input=='Y'){
         count=4;
     }
     if(Input=='A'){
        count=7;
     }
     //I don't know why 528...
     String Send = String(A)+' '+String(X)+' '+String(Y)+' ';
     Serial.println(Send);
     
//     myMotor(A);
//     myServo(X,Y);
     

  }
}

//ServoSpeedX Y 0-100 int
void myServo(int ServoSpeedX, int ServoSpeedY){
  int ServoSpeedmsX = ServoSpeedX*10+1000;
  int ServoSpeedmsY = ServoSpeedY*10+1000;
  // ServoSpeedms Rage 1000-2000
  myservoX.writeMicroseconds(ServoSpeedmsX);  // 1500 to set servo to mid-point
  myservoY.writeMicroseconds(ServoSpeedmsY);  // 1500 to set servo to mid-point
}

//ServoSpeed X 0-100 int
void myServoX(int ServoSpeedX){
  int ServoSpeedmsX = ServoSpeedX*10+1000;
  // ServoSpeedms Rage 1000-2000
  myservoX.writeMicroseconds(ServoSpeedmsX);  // 1500 to set servo to mid-point
}

//ServoSpeed Y 0-100 int
void myServoY(int ServoSpeedY){
  int ServoSpeedmsY = ServoSpeedY*10+1000;
  // ServoSpeedms Rage 1000-2000
  myservoY.writeMicroseconds(ServoSpeedmsY);  // 1500 to set servo to mid-point
}

//MotorSpeed 0-100 int
void myMotor(int MotorSpeed){
  if(MotorSpeed==0){
    mymotor.writeMicroseconds(0);
    }
  else{
    int MotorSpeedms = MotorSpeed*5+1800;
    // MotorSpeedms Rage 1800-2300
    mymotor.writeMicroseconds(MotorSpeedms);
    }
}


// Get int between the indicator char and space from a string
//int GetInt(char indicator, String In){
//  return GotInt;
//  }

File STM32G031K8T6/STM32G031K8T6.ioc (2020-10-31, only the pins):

Mcu.UserName=STM32G031K8Tx
PA1.Signal=SPI1_SCK
PA6.Signal=SPI1_MISO

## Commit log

2020-10-31 PCB TLV62568DBVR
    [PaperPlane.kicad_pcb, PaperPlane.sch]
2020-10-31 PCB sch
    [PaperPlane.kicad_pcb, PaperPlane.sch]
2020-10-31 Add STM32G031K8T6
    [PaperPlane.sch]
2020-11-03 ADD swdio swclk
    [PaperPlane.sch]
2020-11-04 第一次完整程序测试
2020-11-05 Debug Motor
